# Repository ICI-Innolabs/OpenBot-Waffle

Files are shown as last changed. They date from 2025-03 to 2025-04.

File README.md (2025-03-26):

# Welcome to the OpenBot Waffle repository!

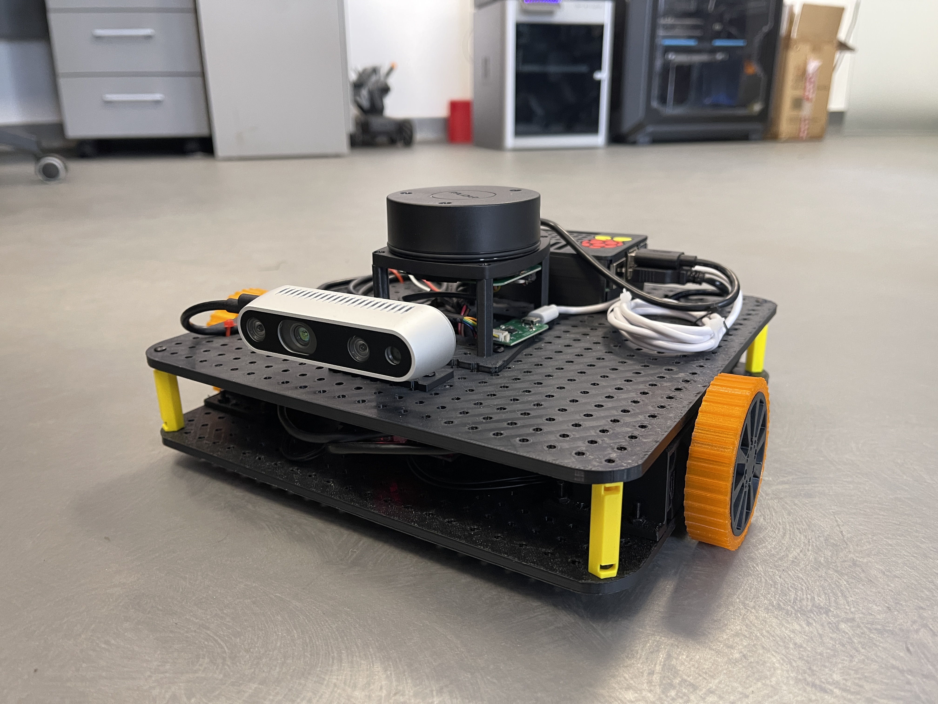
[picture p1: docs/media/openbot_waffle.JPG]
ICIBot Waffle


OpenBot Waffle is a ROS2-based robot platform that can be used for research, education, and hobby purposes. The robot is built around ROS2 and uses a Raspberry Pi 5 as the main controller. The robot is equipped with a Dynamixel XL430-W250-T motor, a Slamtec A1 Lidar, an Adafruit BNO055 IMU, and an Intel RealSense D435i depth camera. The structure of the robot is 3D printed and can be easily assembled. To make things easier when trying new things, the robot can be simulated in Gazebo.

Out of the box, the robot can be controlled via a keyboard or joystick. Also it can also perform SLAM (Simultaneous Localization and Mapping) using Nav2 package from ROS2. 

## 3D Preview

To preview the 3D model of the robot, you can use the following link: [OpenBot Waffle 3D Preview](https://cad.onshape.com/documents/e4455d89093a44267b1c8add/w/d262dbe7157cadda162aa249/e/e17b02729e8f8845fbf66276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)

# Instructions

## Printing and Assembly

To build the OpenBot Waffle robot, you will need to 3D print the components and assemble them. The components list can be found here: [List of Components Needed to Build OpenBot Waffle](docs/component_list.md). The 3D printing and assembly instructions can be found here: [Printing and Assembling Instructions for OpenBot Waffle](docs/3d_printing.md).

## Installation

- After building the physical robot, you will need to install the software on the Raspberry Pi 5. The software installation instructions can be found here: [Software Installation Instructions for OpenBot Waffle](docs/software_installation.md).

- If you are new to ROS2 we recommend you to take a look at the basic instructions here: [ROS2 Basic Instructions](docs/ros2_basic.md).

- When you have ROS2 installed proceed with the next intructions to learn how to launch the robot's main packages and teleoperate the robot: [OpenBot Waffle Basics](docs/teleoperation.md).

## SLAM and Navigation

- To perform SLAM (Simultaneous Localization and Mapping) and start navigation with the robot, you can follow the instructions here: [SLAM and Navigation with OpenBot Waffle](docs/slam.md).

## Gazeebo Simulation

- The robot can be simulated in Gazebo. To simulate the robot in Gazebo, you can follow the instructions here: [Gazebo Simulation for OpenBot Waffle](docs/gazebo_simulation.md).

## Preview of the main packages:

### BNO055_Driver
 - package cloned from https://github.com/the-hive-lab/bno055_driver 
 - to run independently the node that publishes the imu topic: ``` ros2 launch bno055_driver imu.launch.py ``` 
 - publishes in /imu topic

### Dynamixel_Hardware
 - package cloned from https://github.com/dynamixel-community/dynamixel_hardware/tree/jazzy (make sure clone branch jazzy)
 - hardware interface pacage for dynamixel motors
 - used for the dynamixel controller node

### imu_odom_fusion
 - package that fuses the imu and odometry data to publish the robot's pose
 - to run independently the node that publishes the robot's pose: ``` ros2 launch imu_odom_fusion ekf_launch.py ```
 - fusions using extended kalman filters imu readings from imu topic and odometry estimates from odom topic (published by the diff_drive_controller node based on wheel encoders) 
 - publishes in /odometry/filtered topic

### urdf_description
 - package that contains the robot's urdf description, differential drive controller and robot launch files
 - to publish the robot's urdf description: ``` ros2 launch urdf_description urdf_visualize.launch.py ```
 - to launch the robot launch file: ``` ros2 launch urdf_description robot.launch.py ```
    - launches the diff_drive_controller node that publishes the robot's odometry and listens to the cmd_vel topic to control the robot's movement
    - launches the joint_state_publisher node that publishes the robot's joint states
    - can launch the robot_state_publisher node that publishes the robot's tf tree (commented by default)
    - launches joint_state_bridge node that publishes the joint states in the /joint_states topic
    - launches lidar node that publishes the lidar data in the /scan topic (by default from /dev/ttyUSB1)
    - launches the imu_odom_fusion node that fuses the imu and odometry data to publish the robot's pose

### teleop_twist_keyboard
 - package cloned from https://github.com/ros-teleop/teleop_twist_keyboard
 - modified to work with twist stamped messages
 - to run the node that publishes the twist stamped messages: ``` ros2 run teleop_twist_keyboard teleop_twist_keyboard ```

### mapping
 - package that contains the launch file to run cartographer and the configuration files
 - to run cartographer: ``` ros2 launch mapping cartographer.launch.py ```
 - to publish the map: ``` ros2 launch mapping nav2_map_server.launch.py ``` (ignore if use the launch file from localization package)

### localization
 - package that contains the launch file to run amcl and the configuration files
 - to run amcl: ``` ros2 launch localization localizer.launch.py ```

### path_planning
 - package that contains the launch file to run nav2 path planning and the configuration files
 - to run nav2: ``` ros2 launch path_planning path_planner.launch.py ```

### openbot_waffle_gazebo
 - package that contains the launch file to run the gazebo simulation
 - to run the gazebo simulation: ``` ros2 launch openbot_waffle_gazebo robot_description_gazebo.launch.py ```

# License

This project is licensed under the MIT License. See the LICENSE file for details.

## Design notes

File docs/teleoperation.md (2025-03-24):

# Openbot Waffle base packages and teleoperation

This instruction will guide you through the process of getting the robot up and running with the main packages and how to teleoperate the robot via the keyboard or joystick. Also, it will show you how to visualize the robot in RVIZ2.

This project uses ROS2 Control in combination with a custom hardware interface based on the [dynamixel_hardware](https://github.com/dynamixel-community/dynamixel_hardware/tree/jazzy) package that listens for TwistStamped messages on the `/cmd_vel` topic and sends velocity commands to the Dynamixel motors.

## Prerequisites to launch the robot main packages

Firstly on the computer where you will run RVIZ2 launch the robot state publisher node that publishes the robot's tf tree. This can be done by running the following command:

```
ros2 launch urdf_description urdf_visualize.launch.py
```

Then on the Raspberry Pi (robot), launch the robot launch file that starts the diff_drive_controller node that publishes the robot's odometry and listens to the `/cmd_vel` topic to control the robot's movement. This can be done by running the following command:

```
ros2 launch urdf_description robot.launch.py
```

### What does this launch file do?

- Launches the diff_drive_controller node that listens to the `/cmd_vel` topic to control the robot's movement
- Launches the joint_state_publisher node that publishes the robot's joint states to the `/joint_states` topic
- Launches the imu_node that publishes the imu data from BNO055 sensor to the `/imu` topic
- Launches the lidar_node that publishes the lidar data from the RPLidar A1 to the `/scan` topic
- Launches the imu_odom_fusion node that fuses the imu and odometry data to publish the robot's pose to the `/odometry/filtered` topic
- Launches the realsense2_camera node that publishes the RGB and depth images from the RealSense D435 camera
- Launches the tf2_ros static_transform_publisher node that publishes the static transform between the camera and the robot's base_link frame

If all the nodes are launched successfully, you should see the robot's URDF model in RVIZ2 and be able to control the robot using the teleop_twist_keyboard node following the instructions below. If you didn't connect the Lidar or the IMU sensor you should expect to see specific errors in the terminal but the robot should still be able to move. 

### How to visualize the robot in RVIZ2?

To visualize the robot in RVIZ2, run the following command in a new terminal:

```
rviz2
```

When RVIZ2 starts, click on the "Add" button in the bottom left corner of the window and RobotModel. To be able to see the robot set the robot description to /robot_description and the fixed frame to odom. In the next image, you can see the robot in RVIZ2 (refer to the images on the left side to see the settings for the RobotModel).

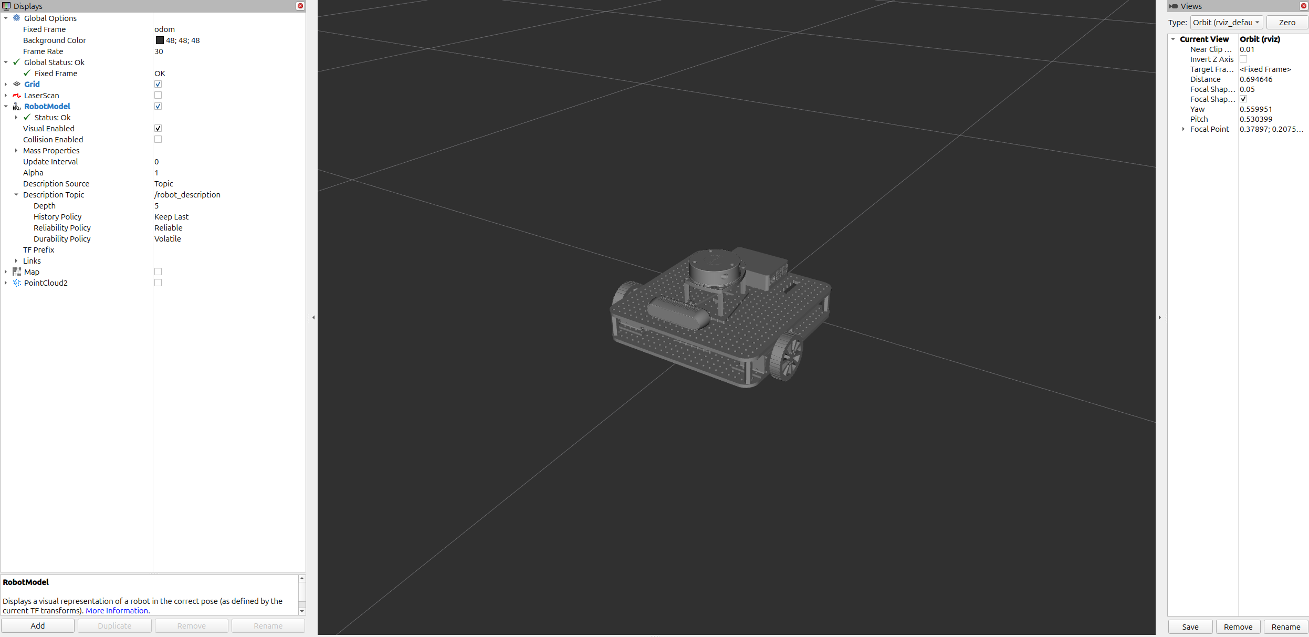
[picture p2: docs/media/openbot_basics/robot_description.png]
OpenBot Waffle in RVIZ2
 

To see the scans from the Lidar, add by topic the lidar scans. To see the camera images, add by topic the PointCloud2 under camera/camera/depth/color/points topic. In the next image you can see the robot along with the lidar scans (pink points) and the camera readings (RGB and depth images) projected in the 3D space.

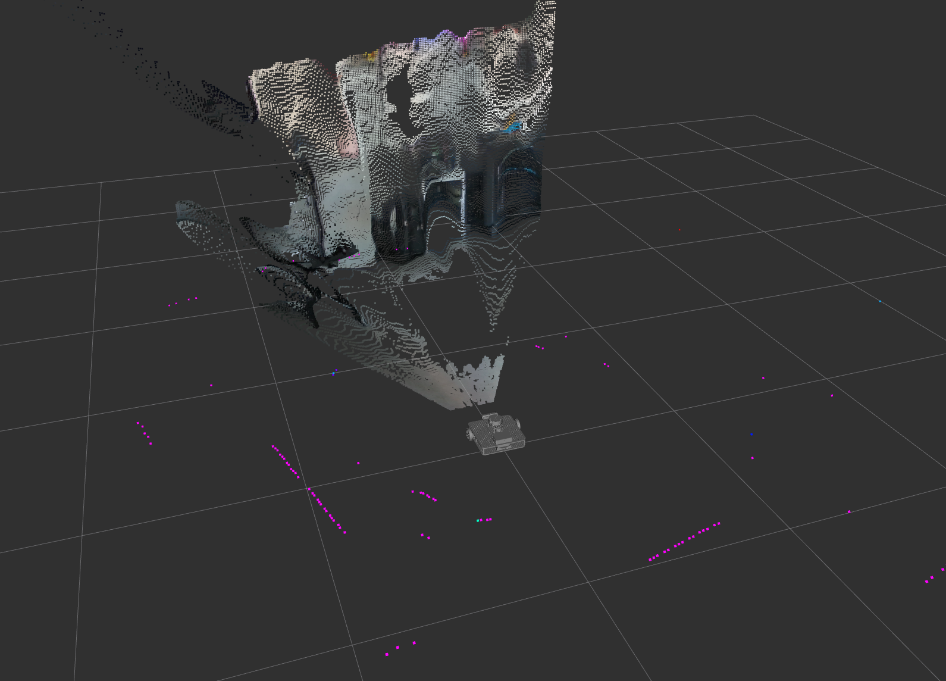
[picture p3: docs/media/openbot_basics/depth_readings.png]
OpenBot Waffle in RVIZ2 with Lidar and Camera
  

## Keyboard Teleoperation

Teleoperation is provided via a modified version of the [teleop_twist_keyboard](https://github.com/ros-teleop/teleop_twist_keyboard) package that now publishes TwistStamped message to control the robot.

To start teleoperating the robot, run the following command in your terminal:

```
ros2 run teleop_twist_keyboard teleop_twist_keyboard
```

When the node starts, use your keyboard according to the on-screen instructions to control the robot. When pressing 'i' the robot will move forward, ',<' to move backward, 'j' to rotate left, and 'l' to rotate right and 'k' to stop the robot.

You can also publish TwistStamped messages directly to the `/cmd_vel` topic to control the robot. For example, to move the robot forward at a linear velocity of 0.1 m/s and an angular velocity of 0.1 rad/s, run the following command:

```
ros2 topic pub /cmd_vel geometry_msgs/msg/TwistStamped '{
  header: {
    stamp: { sec: 0, nanosec: 0 },
    frame_id: ""
  },
  twist: {
    linear: { x: 0.1, y: 0.0, z: 0.0 },
    angular: { x: 0.0, y: 0.0, z: 0.1 }
  }
}'
```

## Joystick Teleoperation

Teleoperation can also be done using a joystick. To start teleoperating the robot with a joystick, run the following command in your terminal:

```
ros2 launch urdf_description diff_drive_control.xacro
```

When the node starts, use your joystick to control the robot. The robot will move according to the left joystick and if you want to move the robot faster (boost mode) you can press R2 button.

This node is inspired from Articulated Robotics. 
 - [Youtube Video](https://www.youtube.com/watch?v=F5XlNiCKbrY)
 - [Github Repository](https://github.com/joshnewans/articubot_one/tree/174b3f311ab146ef12c6549ad0640cb985854972)

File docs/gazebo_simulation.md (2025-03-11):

# Gazebo Simulation

## How to start the simulation

To start the simulation, after building and sourcing the project, simply run the command:
```
ros2 launch openbot_waffle_gazebo robot_description_gazebo.launch.py
```

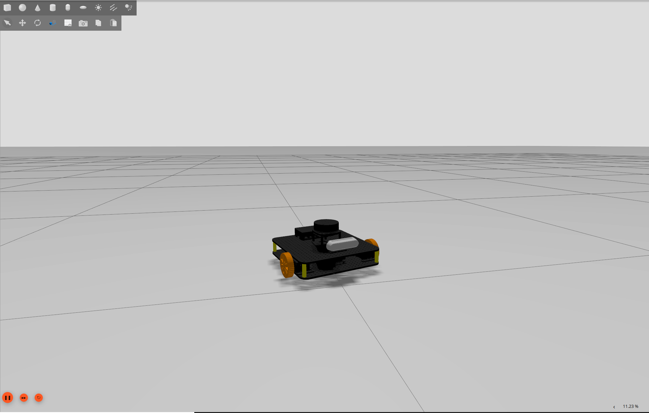
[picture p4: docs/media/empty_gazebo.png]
ICIBot Waffle in empty Gazebo World


- this will launch the Gazebo Simulator and will spawn the OpenBot Waffle into an empty world (as in the  image above)
- it bridges multiple topics from gazebo to ros2 to be able to view in Rviz2 what is the perception of the robot 
- to control the robot using "wasdx" keys from the keyboard, add in gazebo the key publisher from the top right dropdown after searching for it (as in the next image)

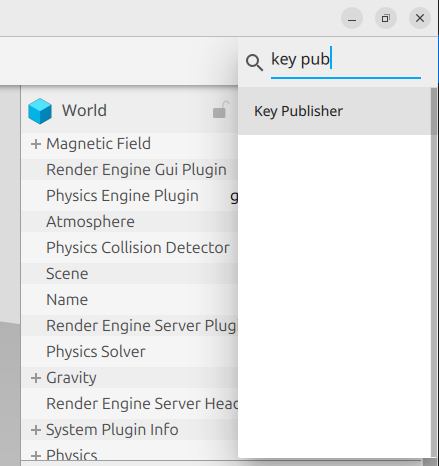
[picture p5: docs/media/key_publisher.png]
Key publisher drop down Gazebo


## Lidar and Depth camera

- similar to the key publisher, lidar visualization can be added in gazebo (do no forget to select the topic where the scans are published, in our case /lidar)
- after adding a few objects into the Gazebo World (similar to next figure), open rviz2 from a new terminal.

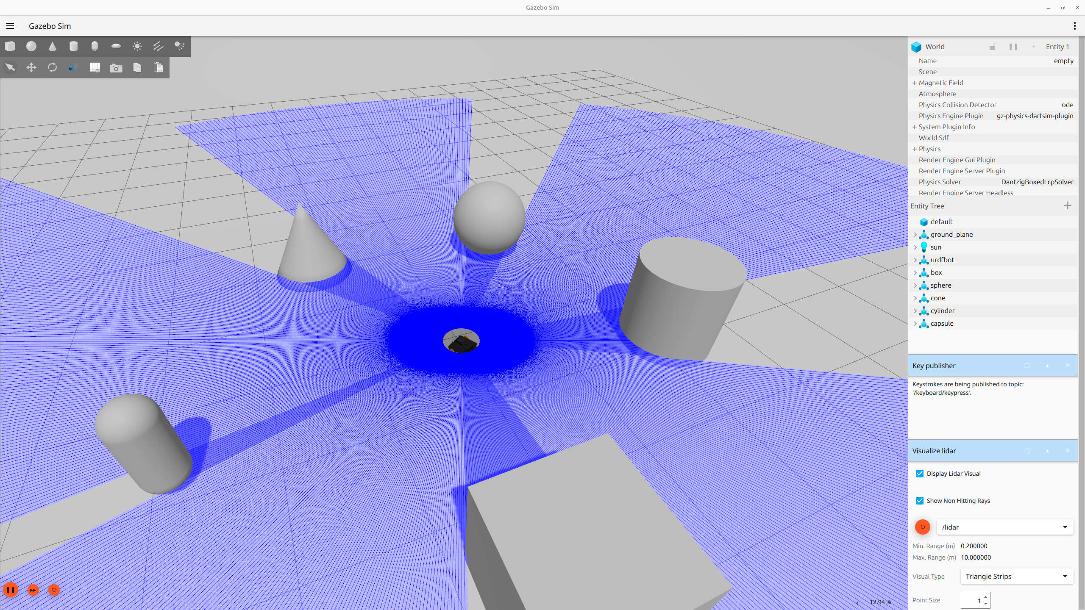
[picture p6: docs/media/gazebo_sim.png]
ICIBot Waffle in empty Gazebo World


- add by topic in rviz2 the PointCloud2 depth readings from the simulated depth camera and the LaserScans from the lidar.

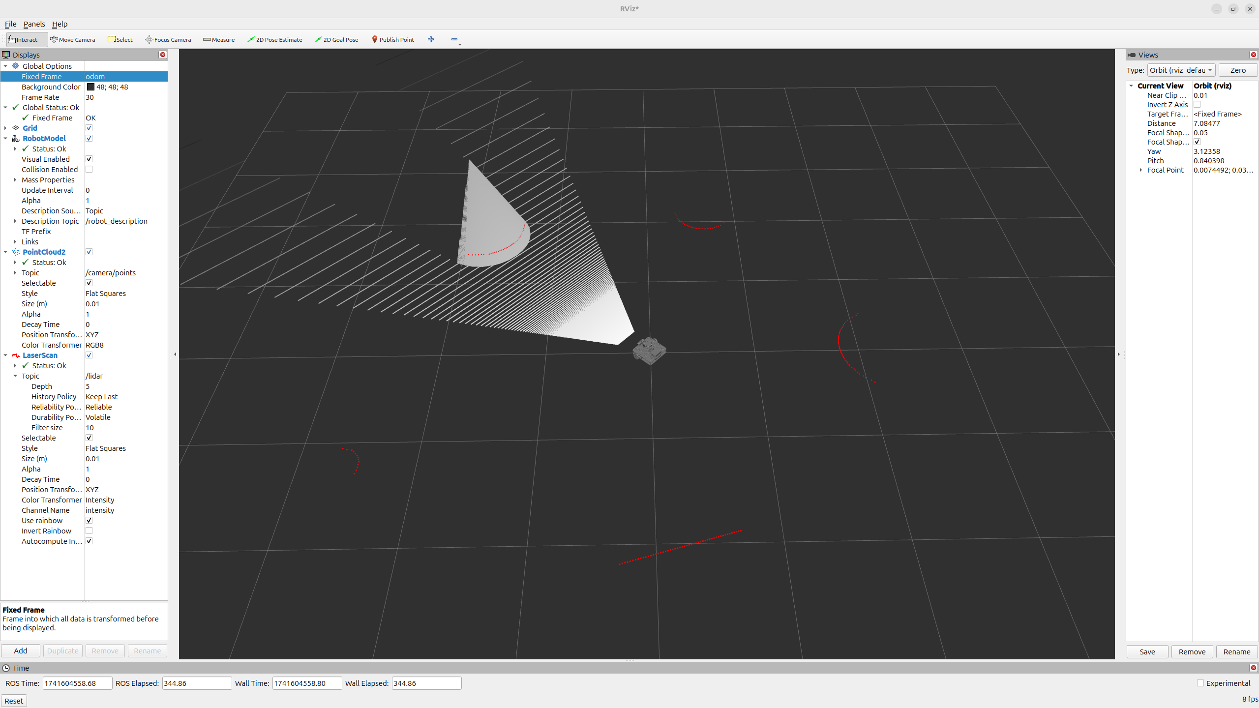
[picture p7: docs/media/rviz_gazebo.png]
Rviz2 Visualization


- you can observe how the readings from the lidar and the depth camera match each other. In our example, the robot is facing the cone and we can see the readings of the lidar are projected as expected on the cone, on level with the lidar of the robot.
- if you move the robot you can observe how the robot moves and the objects remain in the same spots on the visualization (make sure to use as fixed frame /odom in Rviz2)

## Extra

### Gazebo commands

 - To list all the gazebo topic run

```
gz topic -l
```

 - To view the informations about a specific topic (in this case /scan):
 
```
gz topic -t /scan -i
```
 - To echo a topic  (in this case /scan):
 
```
gz topic -t /scan -e
```
 - To publish messages in a topic (in this case in /cmd_vel)
 
```
gz topic -t /cmd_vel -m gz.msgs.Twist -p '
linear: { x: 0.2, y: 0.0, z: 0.0 }
angular: { x: 0.0, y: 0.0, z: 0.0 }'
```

### Bridging

Since we are using Gazebo Sim, to have a topic from ros2 to gazebo or from gazebo to ros2 we have to bridge them manually. When bridging a topic we have to specify the name of the topic and the type of messages (for both ros2 and gz) and the direction of the bridge. The Ros2 and Gz message type correspondets and be viewed [here](https://github.com/gazebosim/ros_gz/blob/ros2/ros_gz_bridge/README.md). Official docs: [here](https://gazebosim.org/docs/latest/ros2_integration/).

to bridge camera topic from gz to ros2: 
```
ros2 run ros_gz_bridge parameter_bridge /camera@sensor_msgs/msg/Image[gz.msgs.Image
```

### More

Official tutorial for simulating a differential steering robot in Gazebo:  https://gazebosim.org/docs/latest/building_robot/

Template for integrating ros2 and gazebo: https://github.com/gazebosim/ros_gz_project_template

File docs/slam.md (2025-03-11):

# Simultaneous Localization and Mapping (SLAM) Example with OpenBot Waffle

## Prerequisites

 - make sure that you've followed the [instructions for teleoperation and robot diff drive control](teleoperation.md) in order to be able to move the robot around

 - publish the robot's urdf description (preferably from external pc to be able to use Rviz2 with higher FPS) with: 
 ``` 
 ros2 launch urdf_description urdf_visualize.launch.py 
 ```

 - launch the robot launch file (directly from raspberry pi): 
 ``` 
 ros2 launch urdf_description robot.launch.py 
 ```

  - make sure thath the robot is publishing the odom topic and the lidar scans. This can be checked by running the next command and looking for /odom and /scans topics 
 ``` 
 ros2 topic list 
 ``` 

 - open a new terminal and launch rviz2: 
 ```
 rviz2 
 ```

 - add the robot model in rviz2 by clicking the Add button and selecting RobotModel. For the moment make sure that the Fixed frame is set to /odom or /base_link.

 - add the LaserScan by topic to visualize the lidar scans.

## Mapping
 - the scope of this is to create the map of the environment where the robot will navigate

 - to launch the cartographer node that will map your environment simply run: 
 ``` 
 ros2 launch mapping cartographer.launch.py 
 ```
 - after launching this node, the robot will start mapping the environment. The map can be visualized in rviz2 by adding the map topic. Make sure that in rviz2 the Fixed frame is set to /map, map topic is set to /map, the history policy to Keep Last, Reliability to Reliable and Durability Policy to Transient Local. In the next image you can see how the map looks when the robot starts mapping the environment. 

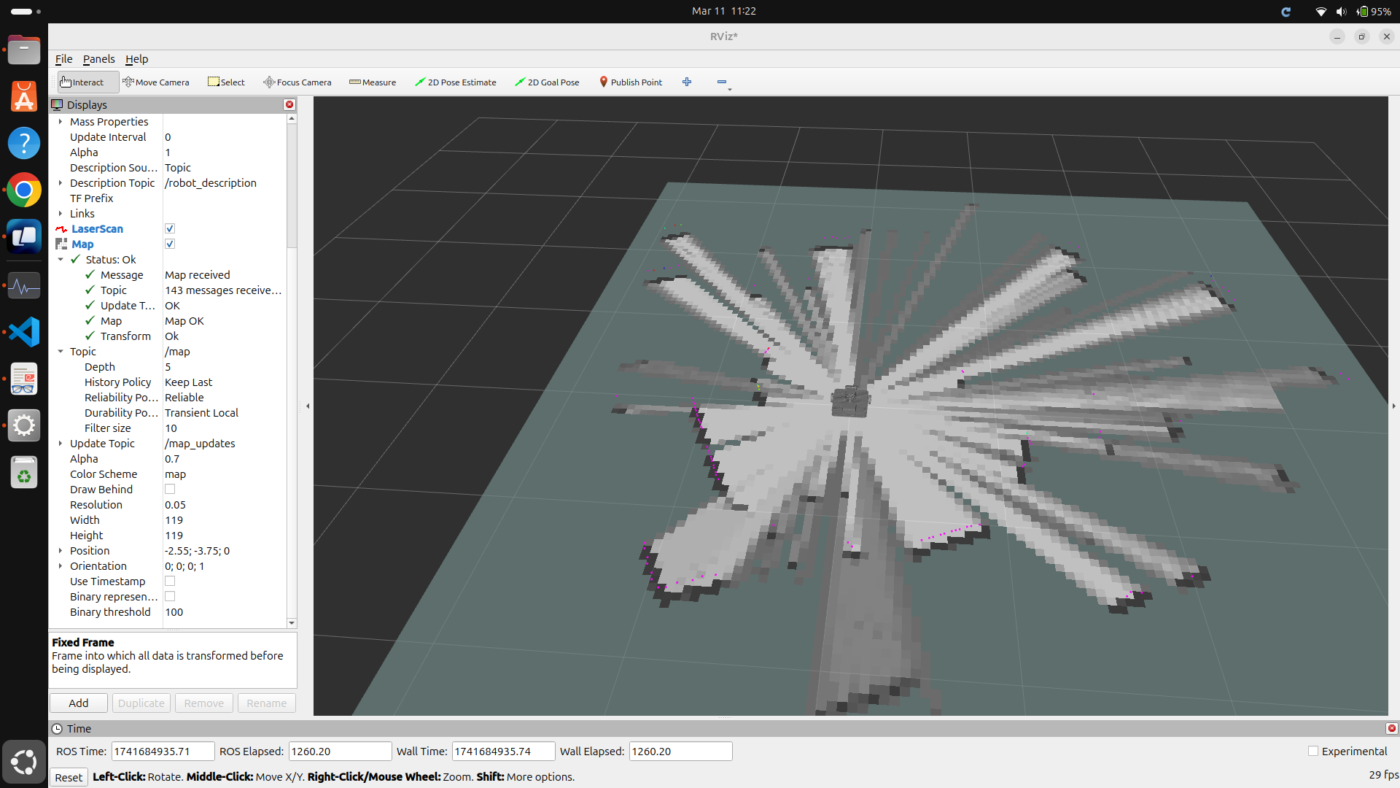
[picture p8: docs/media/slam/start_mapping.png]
Start Mapping Rviz2
 

 - to map the environment the robot needs to moved around. This can be done by teleoperating the robot with the teleop_twist_keyboard node that can be launched with the next command: 
 ``` 
 ros2 run teleop_twist_keyboard teleop_twist_keyboard 
 ``` 

 - after covering the entire environment, the map should look similar to the next image. We suggest to move the robot in a way that the entire environment is covered and have as little as possible dynamic objects in the environment.

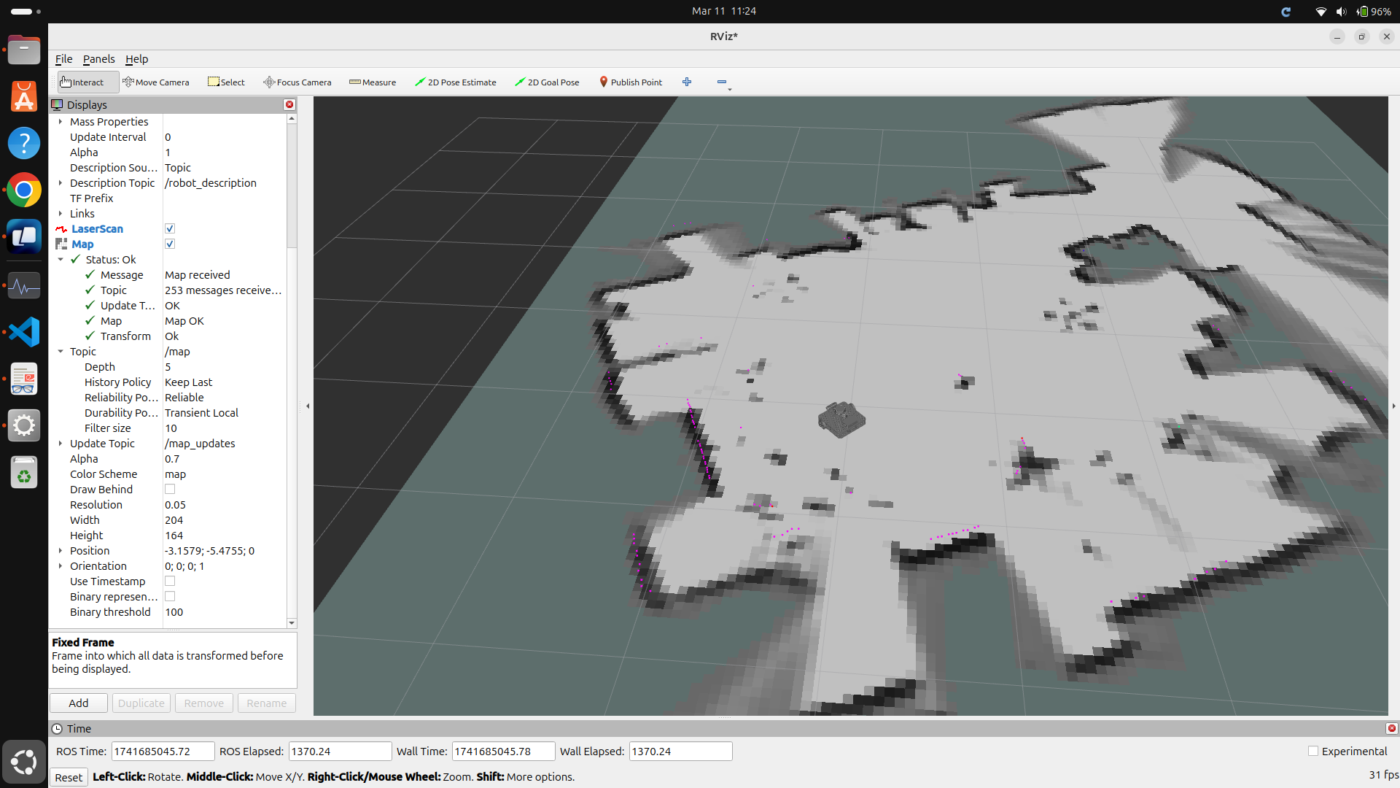
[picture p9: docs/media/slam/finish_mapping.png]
End Mapping Rviz2
  

 - after you've completed mapping the environment, navigate into the config folder inside the mapping package and run the next command to save the map: 
 ``` 
 ros2 run nav2_map_server map_saver_cli -f <path_to_save_map> 
 ```

 - if you want to publish the map this can be done with the following command (ignore if use the launch file from localization package): 
 ``` 
 ros2 launch mapping nav2_map_server.launch.py 
 ``` 

## Localization
 - to localize the robot in the environment, the amcl (Adaptive Monte Carlo Localization) from nav2 package is used.

 - make sure that the name of the saved map is corectly set in the localization package launch file (localizer.launch.py).

 - launch the amcl node: 
 ``` 
 ros2 launch localization localizer.launch.py 
 ```

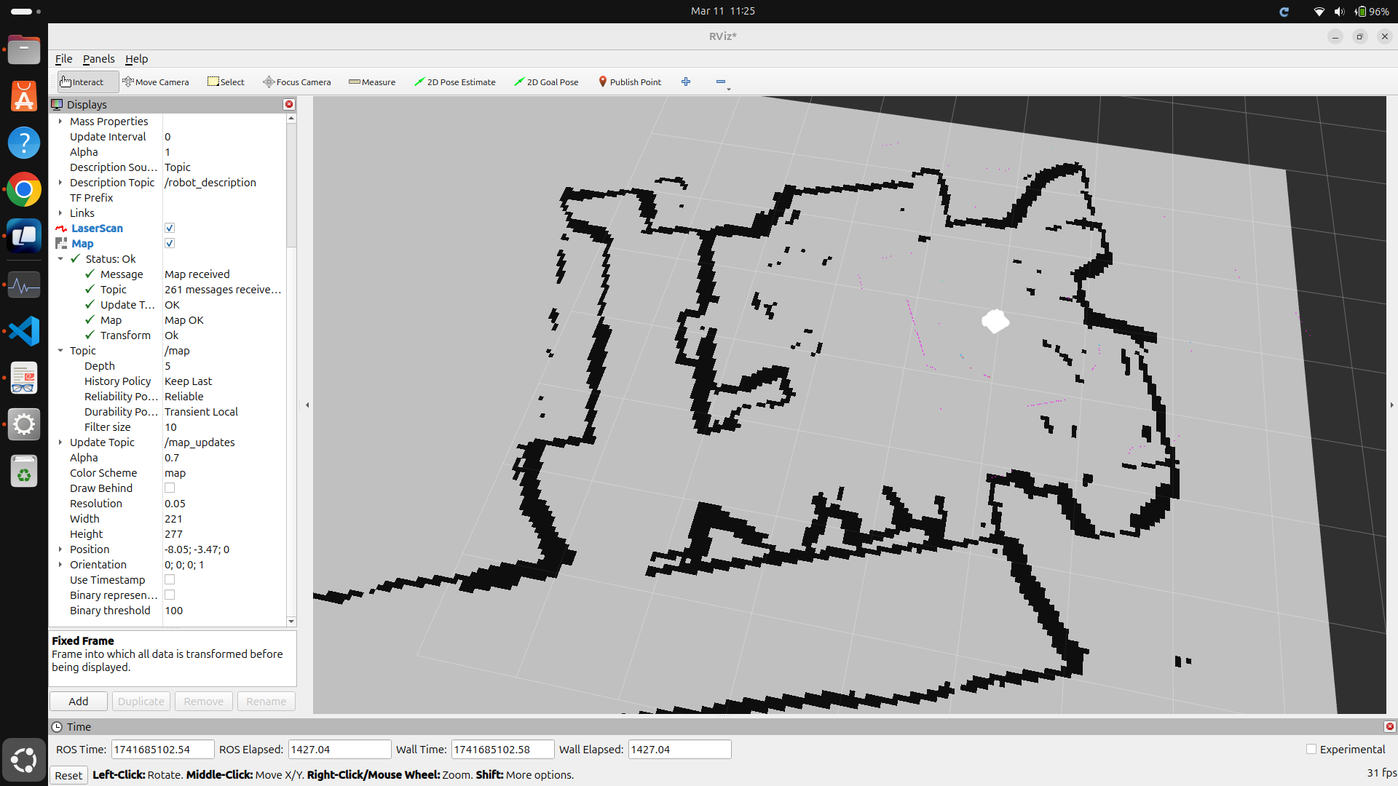
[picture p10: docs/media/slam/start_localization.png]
Start Localization Rviz2
  

 - after launching this node, the robot will wait for the initial pose to be set. This can be done by clicking the 2D Pose Estimate button in rviz2 and setting the initial pose of the robot. Try to set the initial pose as close as possible to the real pose of the robot.

 - after setting the initial pose, the robot will start localizing itself in the environment. The estimated pose can be visualized in rviz2 by adding the PoseWithCovariance by topic. To better localize the robot, you can move the robot around  the environment. After giving the 2D Pose we suggest to simply rotate the robot in place to see how the robot drifts on the map till it localizes itself. When the robot localized itself correctly the lidar scans will match the map (view next image).

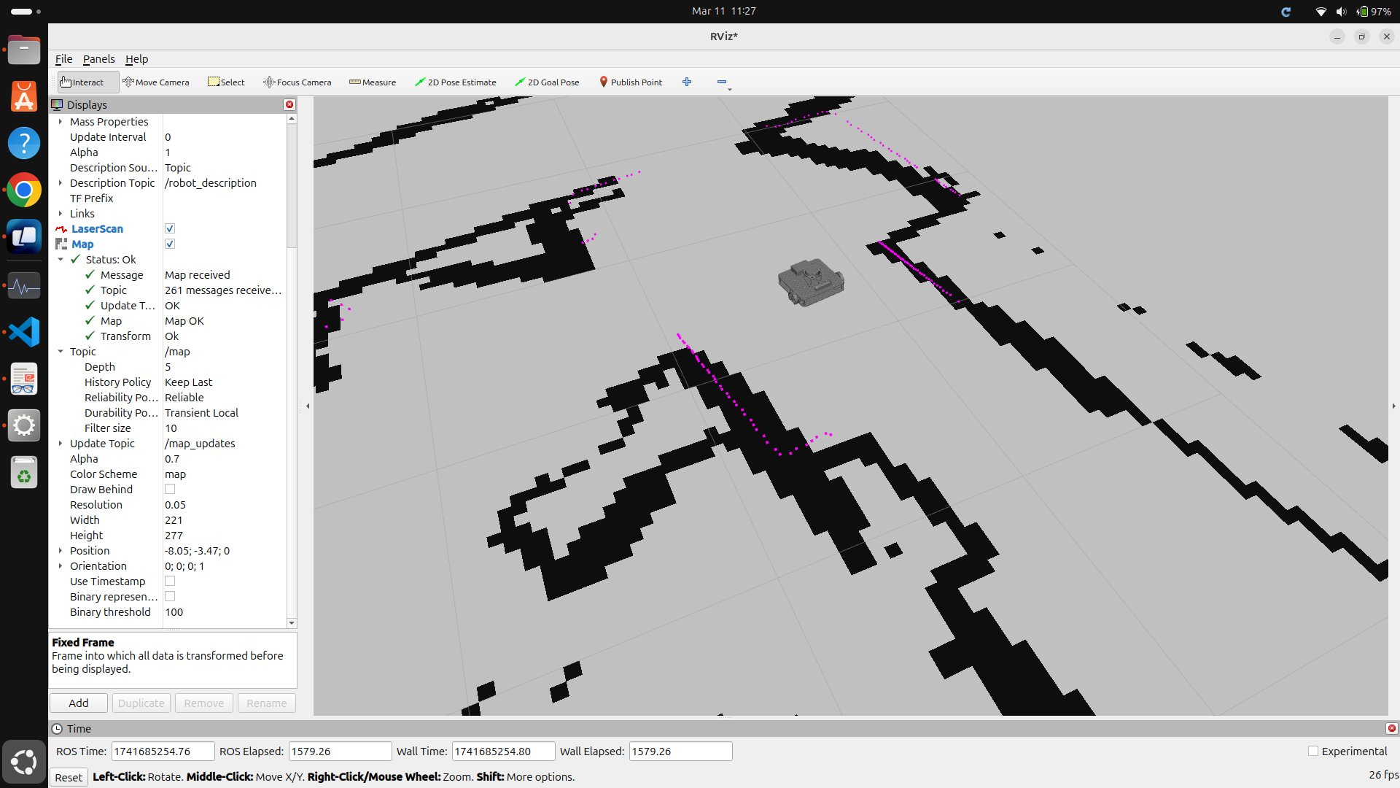
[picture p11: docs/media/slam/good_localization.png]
Good localization Rviz2
  

 - when the robot is localized corectly you can move to the path planning step.

## Path Planning
 - to plan the path for the robot, the nav2 package is used.

 - to run the path planning node: 
 ``` 
 ros2 launch path_planning path_planner.launch.py 
 ```

 - to better view what is happening you can add by topic in Rviz2 the local costmap, global costmap, and the planned path and the goal pose.

 - in the next image can be seen the global costmap (in gray) and the local costmap (in colors)

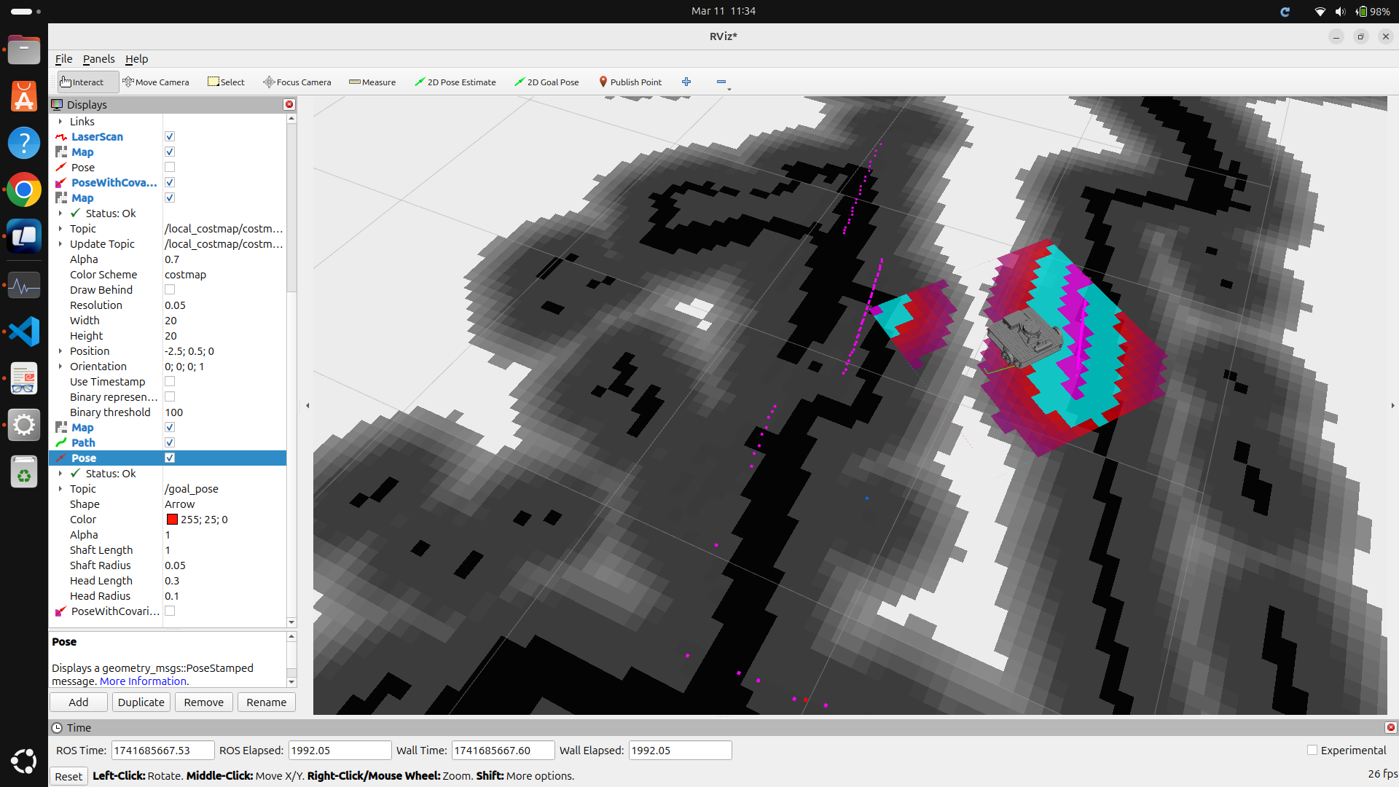
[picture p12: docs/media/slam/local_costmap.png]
Local and Global costmaps in Rviz2
 

 - after launching this node, the robot will wait for the goal to be set. This can be done by clicking the 2D Nav Goal button in rviz2 and setting the goal pose of the robot. Now the robot will start planning the path to the goal and will start moving towards it.

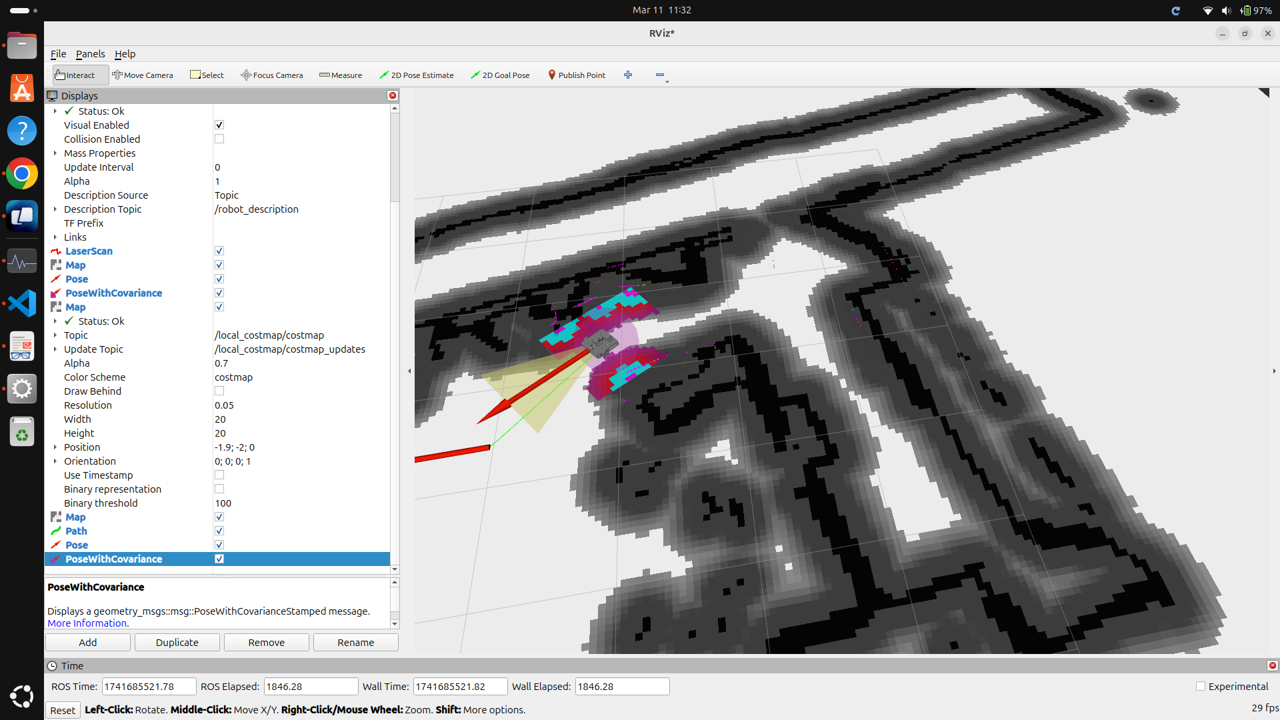
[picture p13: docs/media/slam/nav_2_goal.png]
Navigation to 2D Goal Pose in Rviz2
 

 - in the terminal were you've launched the path planning node, you will see the updated the status of navigation.

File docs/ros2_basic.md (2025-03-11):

# ROS2 Basic commands

Always before running any ROS2 commands, make sure you have sourced both your ROS2 installation and your workspace setup files. In our case, we are using ROS2 Jazzy distribution and the workspace is called `openbot_waffle`. 

``` 
    source /opt/ros/jazzy/setup.bash
    source ~/openbot_waffle/install/setup.bash
```

## Topics

 - to view all active topics in the current ROS2 network, use:
``` 
    ros2 topic list
```

- to inspect the messages being published on a particular topic, use the ros2 topic echo command. For example, to see the output of your lidar data (assuming the topic is named /scan):

``` 
    ros2 topic echo /scan
```

- to get detailed information about a specific topic (including its message type and publisher/subscriber details), use:
``` 
    ros2 topic info /scan
```

- to publish a message on a topic, use the ros2 topic pub command. For example, to publish a message on the /cmd_vel topic (assuming the message type is geometry_msgs/Twist), use:
``` 
    ros2 topic pub /cmd_vel geometry_msgs/Twist '{linear: {x: 0.1, y: 0.0, z: 0.0}, angular: {x: 0.0, y: 0.0, z: 0.1}}'
```

## Nodes

- to view all active nodes in the current ROS2 network, use:
``` 
    ros2 node list
```

- to get detailed information about a specific node (including its name, namespace, and associated topics), use:
``` 
    ros2 node info /node_name
```

- to kill a node, use:
``` 
    ros2 node kill /node_name
```

## Packages

- to list all installed packages in the current ROS2 workspace, use:
``` 
    ros2 pkg list
```

- to create a new python package, use:
``` 
    ros2 pkg create --build-type ament_python package_name
```

- to create a new C++ package, use:
``` 
    ros2 pkg create --build-type ament_cmake package_name
```

- to build a specific package, use:
``` 
    colcon build --packages-select package_name
```

- or alternatively, to build all packages in the workspace, use:
``` 
    colcon build
```

- always remember to source the workspace setup file after building a new package:
``` 
    source ~/openbot_waffle/install/setup.bash
```

## Launch files

- to run a launch file, use:
``` 
    ros2 launch package_name launch_file_name.launch.py
```

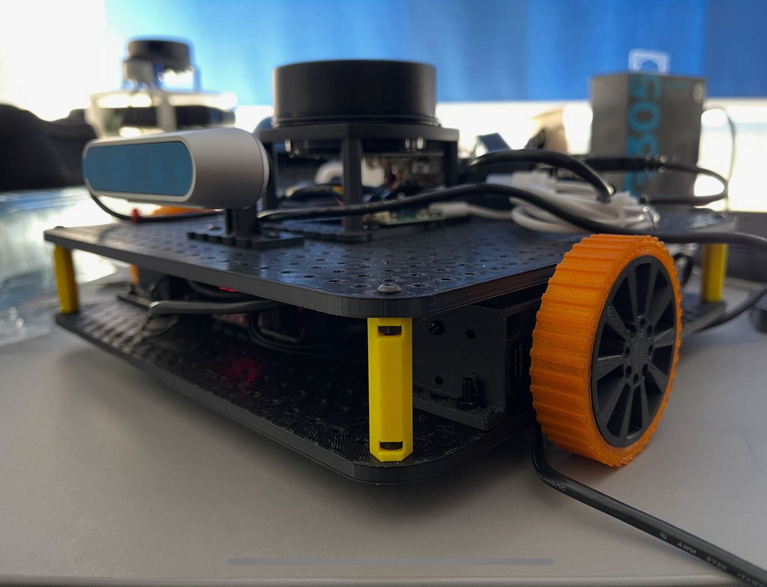
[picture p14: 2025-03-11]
docs/media/icibot_waffle.jpeg

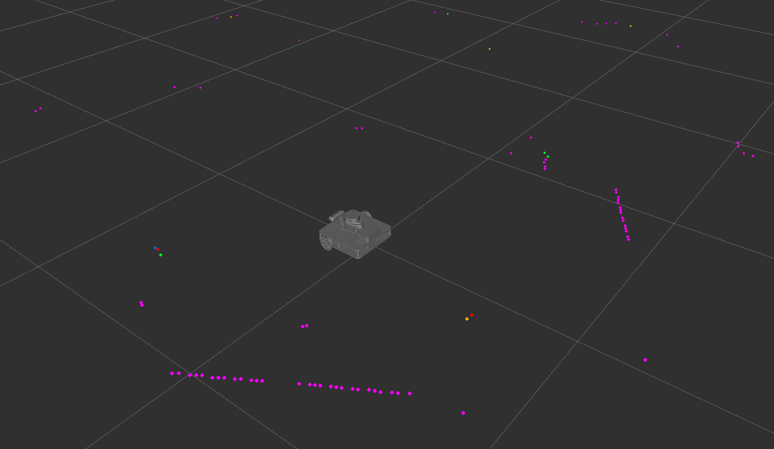
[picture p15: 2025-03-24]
docs/media/openbot_basics/lidar_scans.png

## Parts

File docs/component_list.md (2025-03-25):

# List of Components Needed to Build OpenBot Waffle

| Component | Link | Quantity | Price (single unit) |
| --- | --- | --- | --- |
| Dynamixel XL430-W250 T | [Dynamixel XL430-W250-T Servo](https://www.generationrobots.com/en/402823-dynamixel-xl430-w250-t-servomotor.html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) | 2 | 57 € |
| U2D2 Connector | [U2D2 Dynamixel/PC Connector](https://www.generationrobots.com/en/402820-u2d2-dynamixelpc-connector.html) | 1 | 56 € |
| U2D2 PHB Set | [Génération Robots U2D2 PHB Set](https://www.generationrobots.com/en/403359-u2d2-power-hub-board.html) | 1 | 23 € |
| Raspberry Pi 5 (optimal 8GB version)| [Raspberry Pi 5](https://www.raspberrypi.com/products/raspberry-pi-5/?variant=raspberry-pi-5-8gb) | 1 | 85 € |
| Slamtec A1 Lidar | [RPLIDAR-A1](https://www.slamtec.com/en/lidar/a1) | 1 | 160 € |
| Adafruit BNO055 IMU | [BNO055](https://www.robofun.ro/9-dof-senzor-de-orientare-absoluta-bno055.html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) | 1 | 55 € |
| Depth Camera Intel D435i | [Intel® RealSense™ D435i](https://www.intelrealsense.com/depth-camera-d435i/) | 1 | 400 € |
| 18650 Battery | | 3 | 6 € |
| M3 Screws | | 50 | 5 € |
| M3 Bolts | | 50 | 5 € |
| SD card (at least 32 GB) | | 1 | 10 € |
| 24V/12V to 5V 5A Power Module DC-DC | [Power Module](https://www.optimusdigital.ro/en/step-down-power-supplies/12484-24v12v-to-5v-5a-power-module-dc-dc-xy-3606-power-converter.html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) | 1 | 4 € |

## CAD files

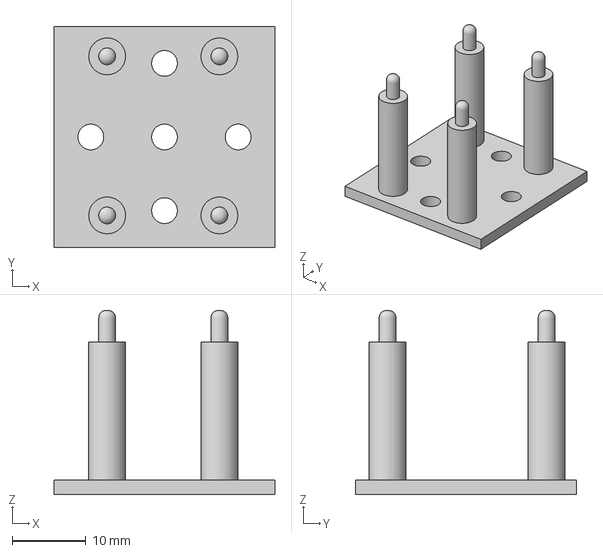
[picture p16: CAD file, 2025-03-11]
3d_files/all_files/IMU Holder.3mf
30.0 x 30.0 x 25.0 mm

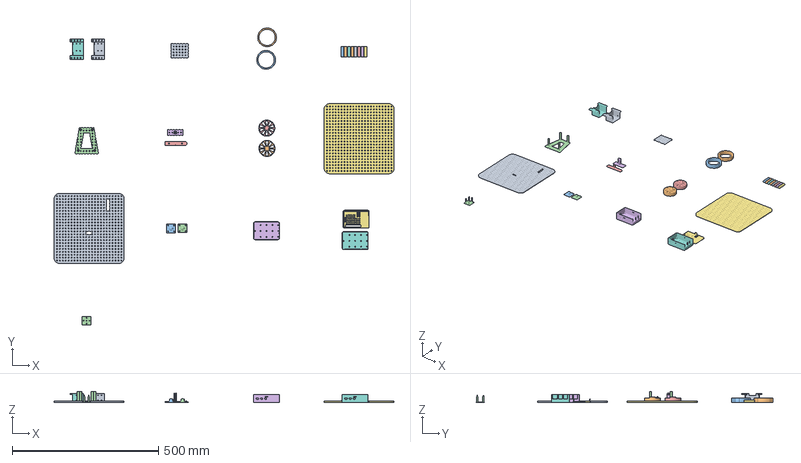
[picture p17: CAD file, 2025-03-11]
3d_files/openbot_waffle_bambu.3mf
1160.7 x 1014.8 x 37.7 mm
U2D2 Holder
tire1 x 2
lidar holder
depth_holder_A
depth_holder_B
baza_lvl_0_B
motor_holder_1 NEW x 2
baza_lvl_0 (1)_B
Distantier_35mm x 8
caster_wheel v1 x 2
rim1_NEW x 2
Caracasa_1 x 2
Carcasa_pi5 v4
IMU Holder

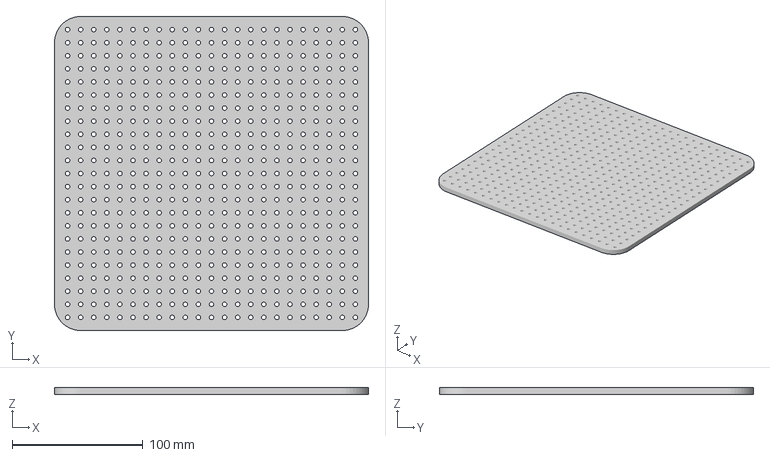
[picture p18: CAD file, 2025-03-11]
3d_files/all_files/base_0.3mf
240.0 x 240.0 x 5.00 mm

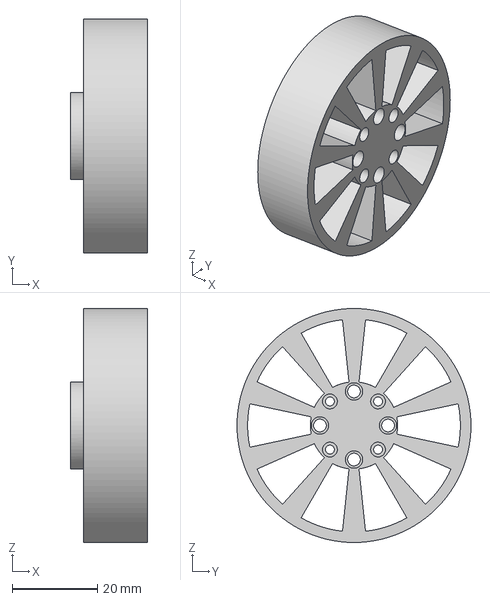
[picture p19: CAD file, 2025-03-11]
3d_files/all_files/rim.3mf
18.0 x 55.0 x 55.0 mm

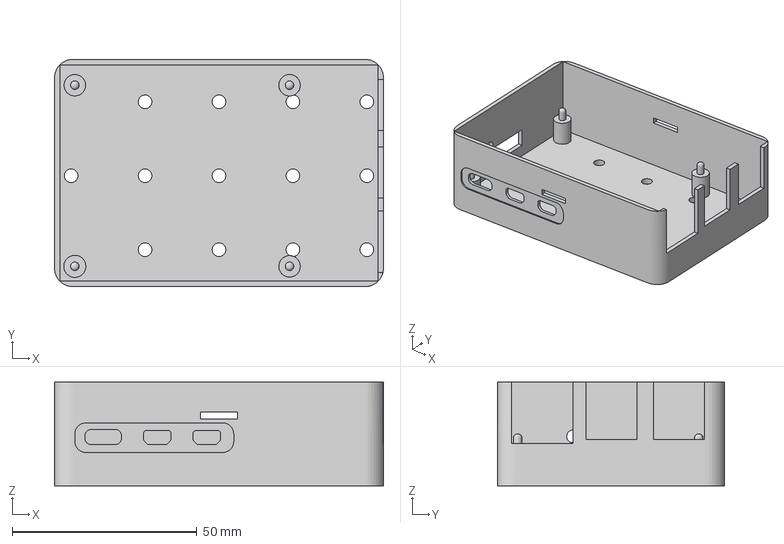
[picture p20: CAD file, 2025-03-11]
3d_files/all_files/pi_case_A.3mf
89.0 x 61.5 x 28.0 mm

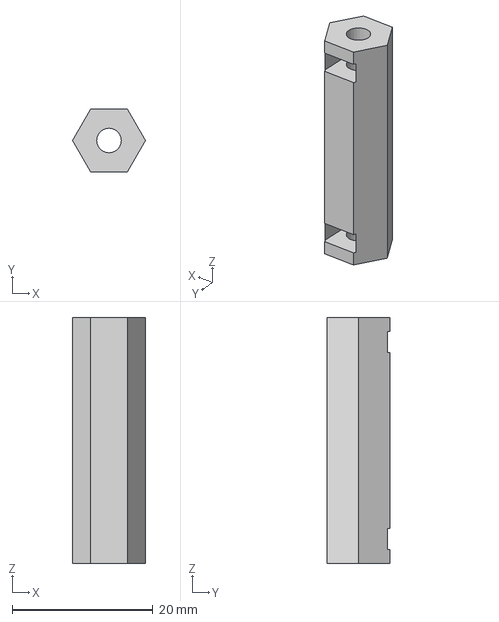
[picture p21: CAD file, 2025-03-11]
3d_files/all_files/spacer_35mm.3mf
10.4 x 9.00 x 35.0 mm

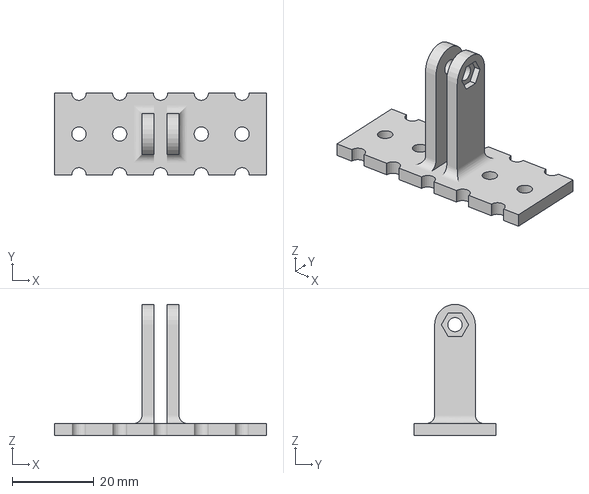
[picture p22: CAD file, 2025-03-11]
3d_files/all_files/dept_holder_B.3mf
52.0 x 20.0 x 32.2 mm

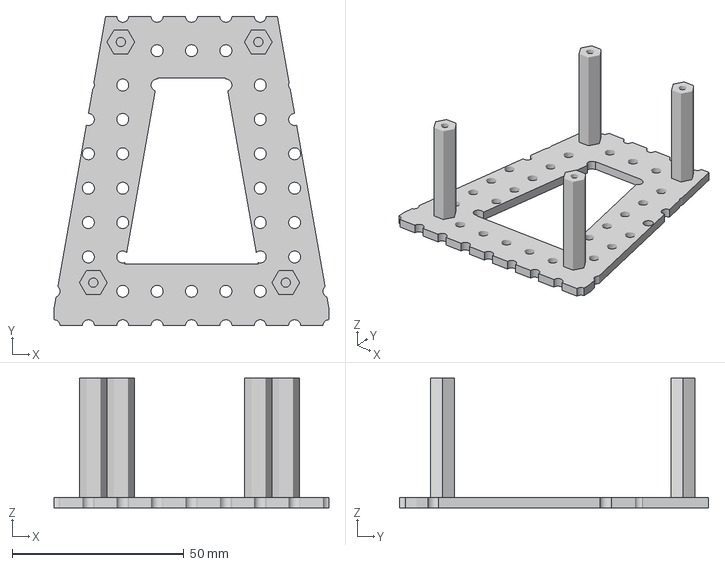
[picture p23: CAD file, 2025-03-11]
3d_files/all_files/lidar_holder.3mf
80.0 x 90.0 x 37.7 mm

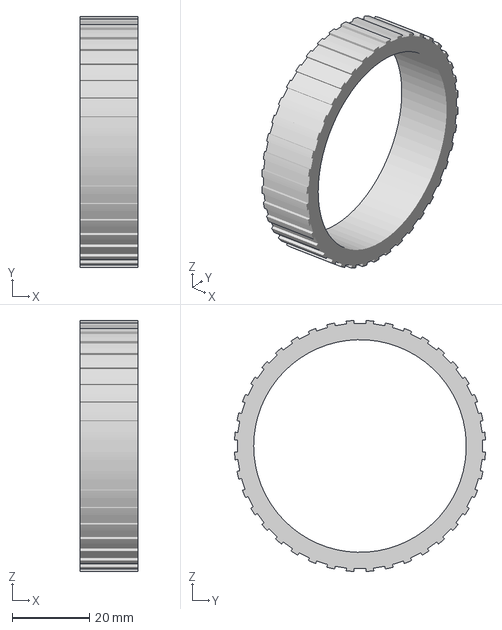
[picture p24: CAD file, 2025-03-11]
3d_files/all_files/tire.3mf
15.0 x 64.9 x 64.9 mm

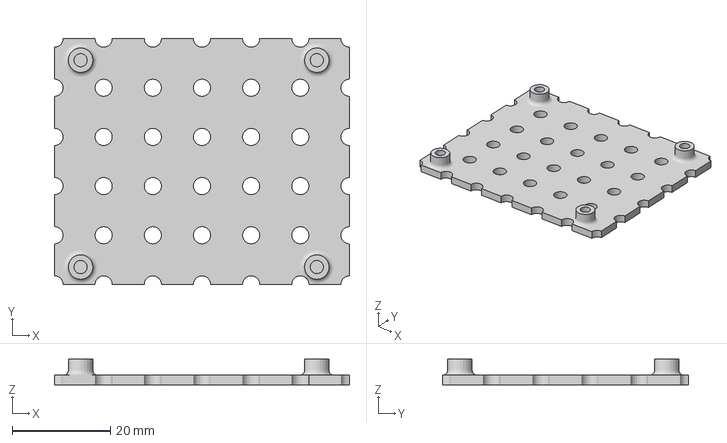
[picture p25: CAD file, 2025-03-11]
3d_files/all_files/holder_u2d2.3mf
60.0 x 50.0 x 5.28 mm

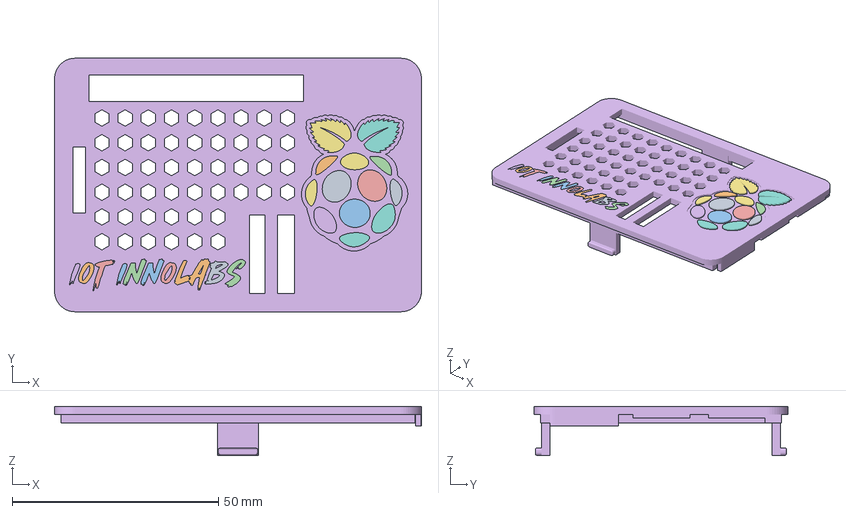
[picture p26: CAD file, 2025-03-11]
3d_files/all_files/pi_case_B.3mf
89.0 x 61.5 x 12.0 mm
Capac_gauri
rpi_frunza (1)
rpi_frunza

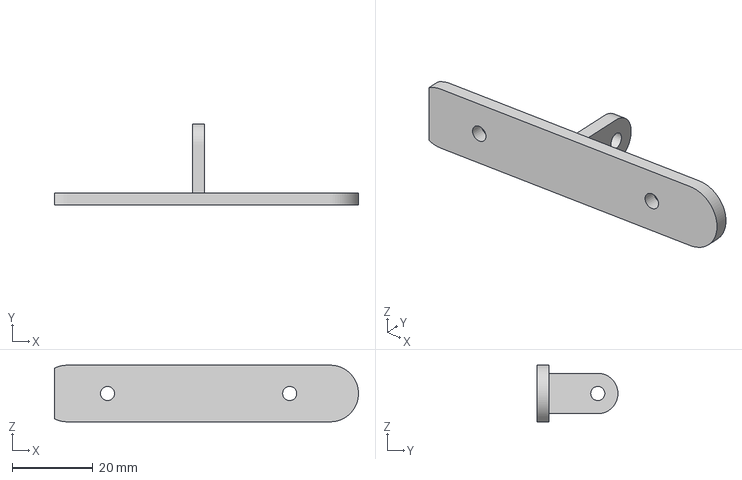
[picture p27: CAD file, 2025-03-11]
3d_files/all_files/depth_holder_A.3mf
75.1 x 20.0 x 14.0 mm

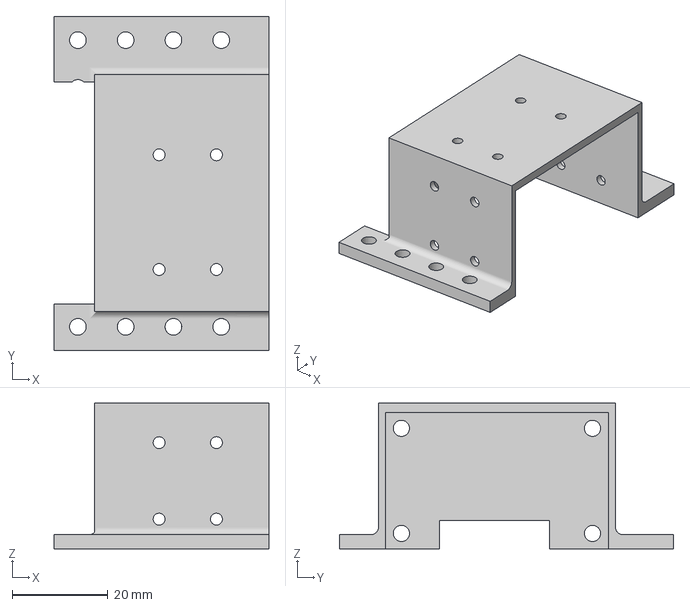
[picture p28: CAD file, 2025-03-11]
3d_files/all_files/xl430_holder.3mf
45.0 x 70.0 x 30.6 mm

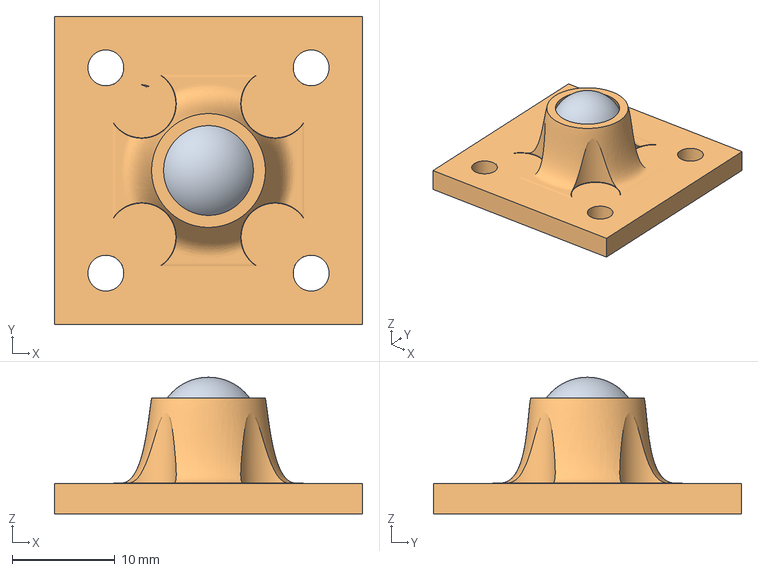
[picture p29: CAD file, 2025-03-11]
3d_files/all_files/caster_wheel.3mf
30.0 x 30.0 x 13.3 mm
object_id_1
object_id_2

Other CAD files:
3d_files/all_files/base1.3mf

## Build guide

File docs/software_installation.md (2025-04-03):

# Software Installation

- Ideally you will be using an external dev machine running Ubuntu 24.04 and ROS2 Jazzy along with the OpenBot Waffle robot that uses a Raspberry Pi 5 running Ubuntu 24.04 and ROS2 Jazzy.
- To install ROS2 Jazzy on Ubuntu 24.04 follow the instructions from the official ROS2 website: [ROS2 Jazzy Installation](https://docs.ros.org/en/jazzy/Installation/Ubuntu-Install-Debs.html)
- Make sure to install the Desktop version of ROS2 Jazzy.
- To install Ubuntu 24.04 on the Raspberry Pi 5, get a new SD card (at least 32 GB), and flash it with Ubuntu using the [Raspberry Pi imager](https://www.raspberrypi.com/software/). After flashing the SD card, insert it into the Raspberry Pi and boot it up. Follow the instructions to set up the Raspberry Pi and proceed with the [installation of ROS2 Jazzy](https://docs.ros.org/en/jazzy/Installation/Ubuntu-Install-Debs.html).
- After installing ROS2 Jazzy, clone the OpenBot Waffle repository to your workspace with the following command:
```
git clone https://github.com/ICI-Innolabs/OpenBot-Waffle.git -b main
```
<!-- - After cloning the repository, also clone the repositories for IMU unit and Dynamixel motors (make sure you clone the jazzy branch) in the `src` folder of your workspace:
```
git clone https://github.com/the-hive-lab/bno055_driver
git clone https://github.com/dynamixel-community/dynamixel_hardware.git -b jazzy
``` -->
- Everything you will run on the Raspberry Pi must be done from the root user. To switch to the root user run the following command (if you will try to launch the node for the imu, it won't work without root permissions):
```
sudo su
```
- Then install the ROS2 packages needed for the OpenBot Waffle robot:
```
sudo apt install ros-jazzy-xacro
sudo apt install ros-jazzy-ros2-control
sudo apt install ros-jazzy-ros2-controllers
sudo apt install ros-jazzy-dynamixel-sdk
sudo apt install ros-jazzy-rplidar-ros
sudo apt install ros-jazzy-joint-state-publisher-gui
sudo apt install ros-jazzy-teleop-twist-keyboard
sudo apt install ros-jazzy-cartographer-ros
sudo apt install ros-jazzy-nav2-amcl
sudo apt install ros-jazzy-nav2-lifecycle-manager
sudo apt install ros-jazzy-nav2-controller
sudo apt install ros-jazzy-nav2-planner
sudo apt install ros-jazzy-nav2-behaviors
sudo apt install ros-jazzy-nav2-bt-navigator
sudo apt install ros-jazzy-nav2-dwb-controller
sudo apt install ros-jazzy-nav2-bringup
sudo apt install ros-jazzy-robot-localization
sudo apt install ros-jazzy-librealsense2*
sudo apt install ros-jazzy-realsense2*
sudo apt install ros-jazzy-dynamixel-workbench-toolbox
sudo apt install ros-jazzy-joint-state-broadcaster
sudo apt install ros-jazzy-diff-drive-controller
sudo apt install ros-jazzy-robot-state-publisher
sudo apt install ros-jazzy-ros-gz-sim
sudo apt install ros-jazzy-ros-gz-bridge
sudo apt install ros-jazzy-nav2-map-server
```

- To install the python packages needed for the OpenBot Waffle, run the following command:
```
pip install -r requirements.txt --break-system-packages
```

## Dynamixel Motors configuration

- To configure the Dynamixel motors firstly connect the motors individually to the U2D2 module and connect the U2D2 to a machine with Dynamixel Wizard 2.0 installed.
- After connecting the first motor change its ID to 1 and the baud rate to 57600.
- Disconnect the first motor then connect the second motor, change its ID to 2 and the baud rate to 57600.
- Since the motors will be mirrored, it is possible to have one motor spinning in the opposite direction. To fix this, change the motor's spinning direction by ticking the box for Bit 0 - Reverse mode under the Drive mode tab.
- On the Raspberry Pi, configure the latency_timer to 1 instead of 16 by running the following commands or following the instructions form the [official documentation](https://emanual.robotis.com/docs/en/parts/interface/u2d2/#linux).
```
cat /sys/bus/usb-serial/devices/ttyUSB0/latency_timer
echo 1 > /sys/bus/usb-serial/devices/ttyUSB0/latency_timer
cat /sys/bus/usb-serial/devices/ttyUSB0/latency_timer
```
- After configuring the motors, connect them to the U2D2 module and connect the U2D2 module to the Raspberry Pi and test the motors. If the motors aren't operating as expected use the python scripts from the `extra/test_motors` folder to identify the issue.

## Configuration for D435I Depth camera

- Since we are using a custom power supply for the Raspberry Pi, by default the USB ports are limited to 0.6A. To increase the current limit to 1.6A run the following command:
```
sudo nano /boot/firmware/config.txt
```
- And add the following line at the end of the file:
```
usb_max_current_enable=1
```
- After adding the line, save the file by pressing `Ctrl + X`, then `Y` and then `Enter` and reboot the Raspberry Pi by running the following command:
```
sudo reboot
```

## Extra - ROS2 Jazzy Installation with Docker

- If you don't have a machine with Ubuntu 24.04, you can use Docker to create a container with ROS2 Jazzy.
- After installing docker you can follow this [guide](https://docs.ros.org/en/jazzy/How-To-Guides/Installing-on-Raspberry-Pi.html)

<!-- - to get both lidar and depth camera working. firstly launch robot launch (withouth the depth camera plugged in) then plug in depth camera and launch d435i node with: -->

<!-- - To publish the depth image from the D435I camera run the following command:
```
ros2 run realsense2_camera realsense2_camera_node
```

- In RVIZ2 you can visualize the depth image by adding a new image topic and selecting the `/camera/camera/depth/image_rect_raw` topic.

- useful links: https://github.com/IntelRealSense/realsense-ros and https://dev.intelrealsense.com/docs/ros2-pointcloud-examples -->

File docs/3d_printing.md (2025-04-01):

# Printing and assembling instructions for OpenBot Waffle

- To preview the 3D model of the robot, you can use the following link: [OpenBot Waffle 3D Preview](https://cad.onshape.com/documents/e4455d89093a44267b1c8add/w/d262dbe7157cadda162aa249/e/e17b02729e8f8845fbf66276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)

# 3D Priting

The files needed for 3D printing the OpenBot Waffle robot are available in the `3d_files` folder. 

## Files `base0` and `base1` can be printed only with printers with build plate of at least 256 x 256 mm. 

For 3D printing we've used a BambuLab X1C printer. If you are using a BambuLab printer (A1, P1S or X1C) you can open `openbot_waffle_bambu.3mf` with Bamabu Studio and start printing. For the tires you have to use TPU filament and for the rest of the parts PLA filament. 

If you are using a different printer, in the `all_files` subfolder you can find all the parts in 3mf format. Print the tires with TPU filament and the rest of the parts with PLA filament. The only pieces that need supports are rims and the XL430 holders. 

If you are printing each parts individually use the next table to know the quantity of each part needed:

| Part Name | Quantity |
| --- | --- |
| `base0` | 1 |
| `base1` | 1 |
| `caster_wheel` | 2 |
| `rim` | 2 |
| `tire` | 2 |
| `xl430_holder` | 2 |
| `spacer_35mm` | 6 |
| `depth_holder_A` | 1 |
| `depth_holder_B` | 1 |
| `holder_u2d2` | 1 |
| `lidar_holder` | 1 |
| `imu_holder` | 1 |
| `pi_case_A` | 1 |
| `pi_case_B` | 1 |

# Assembly - Start after printing all the parts

 ## Step 1 - Attach components to their holders

 - Fix the Dynamixel XL430 motors in the XL430 holders with the screws provided with the motors.
 - Glue the tires to the rims.
 - Fix the wheels to the motors with the screws provided with the motors (4 screws is enough).
 - Attach the IMU unit to the IMU holder (before fixing the imu to the holder, connect 4 arduino cables to the IMU, red to Vin, black to GND and other two to SCL and SDA pins).
 - Attach depth holder A and B with a screw and nut then fix the depth camera to the holder.
 - Attach the Lidar to the lidar holder.

## Step 2 - Fix the components on the bottom base plate

 - Both for base0 and base1, to fix the parts in the exact position, refer to the [3D model of the robot](https://cad.onshape.com/documents/e4455d89093a44267b1c8add/w/d262dbe7157cadda162aa249/e/e17b02729e8f8845fbf66276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)
 - Using 3mm screws and nuts fix the motors, imu (before fixing it attach 4 cables to its VCC, SCL, SDA and GND pins), battery holder and u2d2 module to the base0 part.
 - Connect the motors to the U2D2 module, in the next image you can see how the Dynamixel motors are wired to the U2D2 module. Leave a USB cable connected to the U2D2 module that later will be connected to the Raspberry Pi.
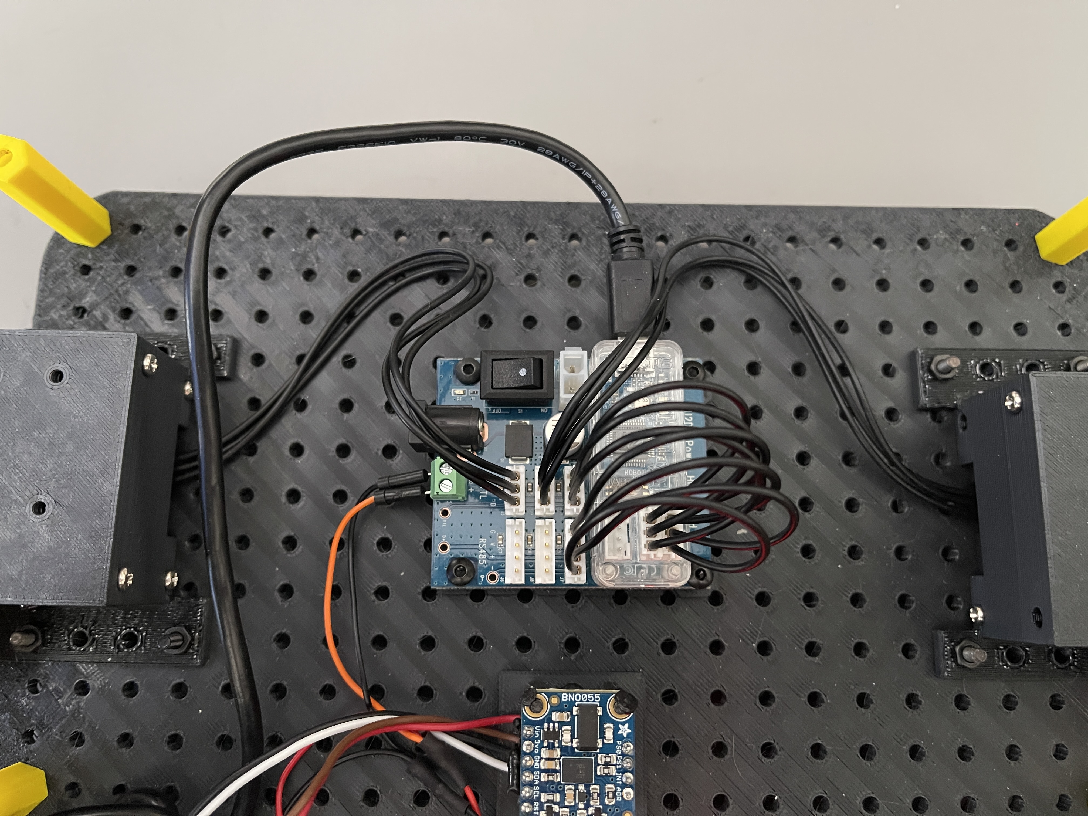
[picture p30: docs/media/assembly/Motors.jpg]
    
 - Glue the 5V 5A step down module to the base0 part.
 - Use zip ties to fix the cables to the plate.
 - Connect the battery holder to the 5V 5A step down module and to the U2D2 module. Leave an USB to Type C cablle connected to the 5V 5A step down module that later will power the Raspberry Pi. 
 - Make sure that the U2D2 module is powered directly from the battery since it needs 12 V to operate. If you power it from the 5V 5A step down module, it won't work.

 - Using 3mm screws and nuts fix the two caster wheels and six spacers to the base0 part.
 - After fixing all the components on the bottom plate, it should look like this:
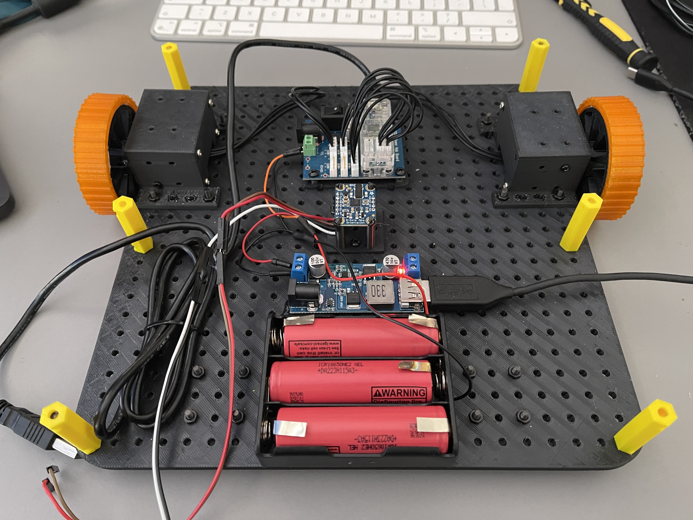
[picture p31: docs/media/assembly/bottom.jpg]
    

## Step 3 - Assemble the top plate of the robot

 - Screw on the base1 part the depth camera and lidar.
 - Fix on the base1 the raspberry pi holder then fix the raspberry pi to the holder.
 - Use zip ties to fix the cables from the lidar and depth camera to the plate.
 - Connect the Lidar and Depth camera to the Raspberry Pi via USB.
 - In the next image you can see how the top plate of the robot should look like.
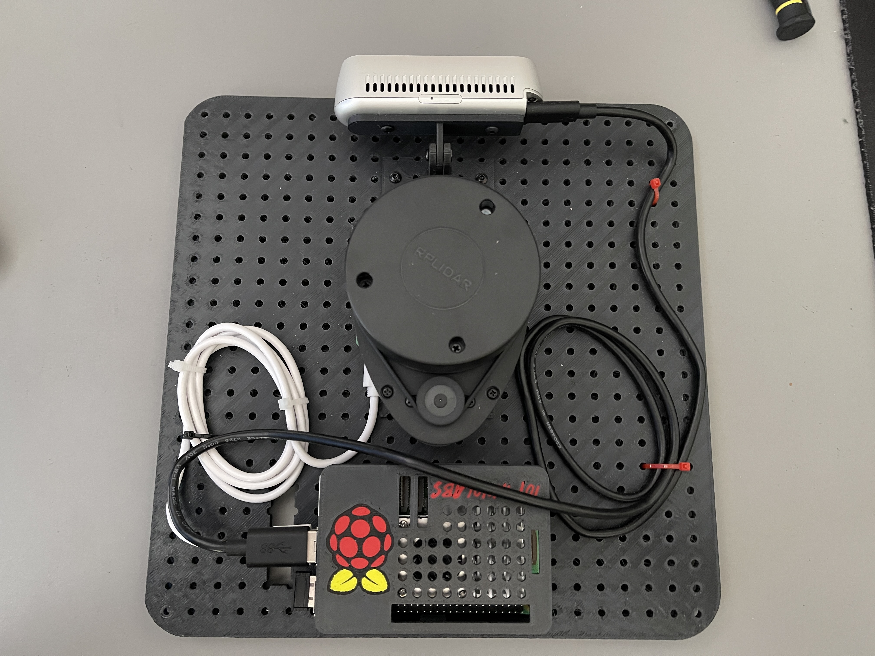
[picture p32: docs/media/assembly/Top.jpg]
      

 ## Step 4 - Assemble the robot by connecting the top and bottom plates via the spacers

 - Connect the base0 part to the base1 part with screws and nuts via the spacers. Pass the arduino cables (for the IMU) and the Type C cable through the hole of the base1 part (the hole under the lidar). Pass the cable from the U2D2 module through the hole of the base1 part (the hole next to the Raspberry Pi USB ports).
 - Connect the IMU to the Raspberry Pi following the next image. Use the hole from the upper base to pass the cables.
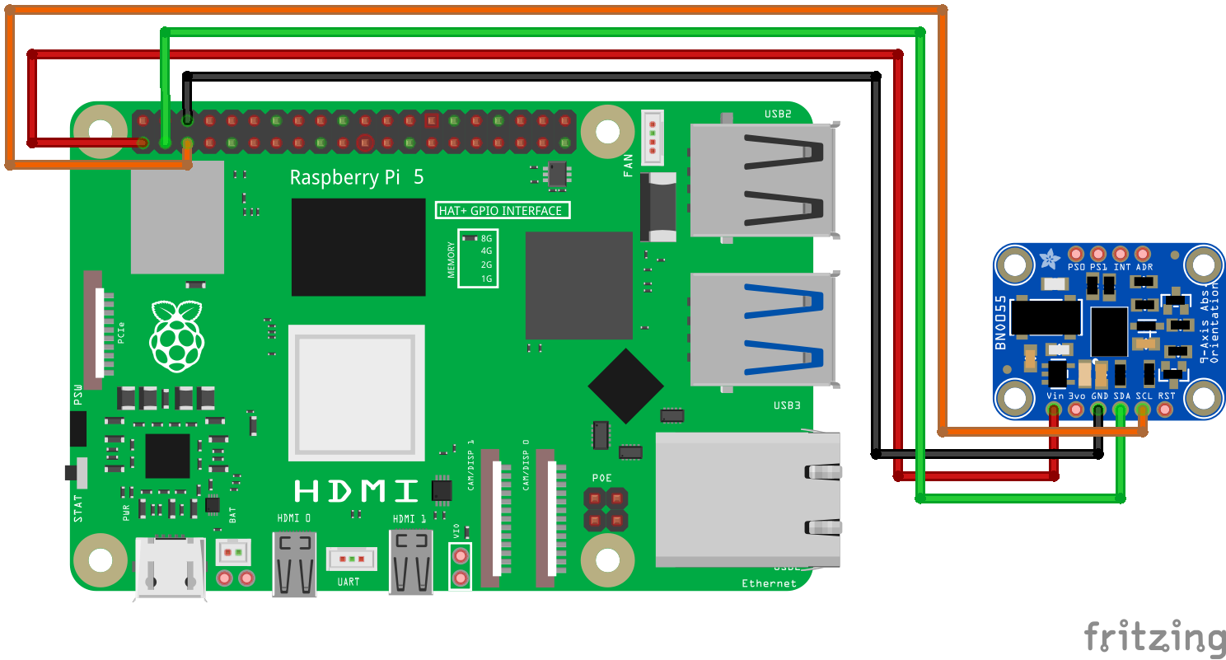
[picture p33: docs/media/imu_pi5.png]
 
 - Connect the U2D2 module to the Raspberry Pi via USB.

## Extra

 - When you are not using the robot, do not forget to remove the type C cable that powers it (even if you've turned off the raspberry pi). If you leave it connected, the battery will be drained in a few days (or even hours).

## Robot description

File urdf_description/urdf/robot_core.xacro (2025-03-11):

<?xml version="1.0"?>
<robot name="urdfbot" xmlns:xacro="http://ros.org/wiki/xacro">

  <xacro:property name="scl" value="0.001"/>
  <xacro:property name="PI" value="3.14159265335897931" />

    <link name="base_link">
    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
    <inertial>
      <mass value="10"/>
      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
    </inertial>
  </link>

  <link name="motor_left">
    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
    <inertial>
      <mass value="0.05"/>
      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
    </inertial>
  </link>

  <joint name="base_link_to_motor_left" type="fixed">
    <origin xyz="0.06 0.1 0.005" rpy="0 0 ${PI/2}"/>
    <parent link="base_link"/>
    <child link="motor_left"/>
  </joint>

  <link name="motor_right">
    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
    <inertial>
      <mass value="0.05"/>
      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
    </inertial>
  </link>

  <joint name="base_link_to_motor_right" type="fixed">
    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
    <origin xyz="0.06 -0.1 0.005" rpy="0 0 ${PI/2}"/>
    <parent link="base_link"/>
    <child link="motor_right"/>
  </joint>

  <link name="left_wheel">
    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
    <inertial>
      <mass value="0.05"/>
      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
    </inertial>
  </link>

  <joint name="motor_left_to_left_rim" type="continuous">
    <origin xyz="0.021 0.01 0.01425" rpy="0 0 0"/>
    <axis xyz="1 0 0"/>
    <parent link="motor_left"/>
    <child link="left_wheel"/>
  </joint>

  <link name="right_wheel">
    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
    <inertial>
      <mass value="0.05"/>
      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
    </inertial>
  </link>

  <joint name="motor_right_to_right_rim" type="continuous">
    <origin xyz="-0.021 0.01 0.01425" rpy="0 0 0"/>
    <axis xyz="1 0 0"/>
    <parent link="motor_right"/>
    <child link="right_wheel"/>
  </joint>

  <link name="caster_wheel_left">
    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
    <inertial>
      <mass value="0.01"/>
      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
    </inertial>
  </link>

  <joint name="base_link_to_caster_wheel_left" type="fixed">
    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
    <origin xyz="-0.09 0.06 0" rpy="0 0 0"/>
    <parent link="base_link"/>
    <child link="caster_wheel_left"/>
  </joint>

  <link name="caster_wheel_right">
    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
    <inertial>
      <mass value="0.01"/>
      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
    </inertial>
  </link>

  <joint name="base_link_to_caster_wheel_right" type="fixed">
    <origin xyz="-0.09 -0.06 0" rpy="0 0 0"/>
    <parent link="base_link"/>
    <child link="caster_wheel_right"/>
  </joint>

  <link name="u2d2_link">
    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
  </link>

  <joint name="base_link_to_u2d2_link" type="fixed">
    <origin xyz="0.05 0 0.005" rpy="0 0 0"/>
    <parent link="base_link"/>
    <child link="u2d2_link"/>
  </joint>

  <link name="battery_link">
    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
    <inertial>
      <mass value="0.15"/>
      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
    </inertial>
  </link>

  <joint name="base_link_to_battery_link" type="fixed">
    <origin xyz="-0.08 0 0.005" rpy="0 0 0"/>
    <parent link="base_link"/>
    <child link="battery_link"/>
  </joint>

  <link name="spacer_front_right_lvl_0">
    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
  </link>

  <joint name="base_link_to_spacer_front_right_lvl_0" type="fixed">
    <origin xyz="0.11 -0.11 0.005" rpy="0 0 0"/>
    <parent link="base_link"/>
    <child link="spacer_front_right_lvl_0"/>
  </joint>

  <link name="spacer_middle_right_lvl_0">
    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
  </link>

  <joint name="base_link_to_spacer_middle_right_lvl_0" type="fixed">
    <origin xyz="0 -0.11 0.005" rpy="0 0 0"/>
    <parent link="base_link"/>
    <child link="spacer_middle_right_lvl_0"/>
  </joint>

  <link name="spacer_back_right_lvl_0">
    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
  </link>

  <joint name="base_link_to_spacer_back_right_lvl_0" type="fixed">
    <origin xyz="-0.11 -0.11 0.005" rpy="0 0 0"/>
    <parent link="base_link"/>
    <child link="spacer_back_right_lvl_0"/>
  </joint>

  <link name="spacer_front_left_lvl_0">
    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
  </link>

  <joint name="base_link_to_spacer_front_left_lvl_0" type="fixed">
    <origin xyz="0.11 0.11 0.005" rpy="0 0 0"/>
    <parent link="base_link"/>
    <child link="spacer_front_left_lvl_0"/>
  </joint>

  <link name="spacer_middle_left_lvl_0">
    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
  </link>

  <joint name="base_link_to_spacer_middle_left_lvl_0" type="fixed">
    <origin xyz="0.0 0.11 0.005" rpy="0 0 0"/>
    <parent link="base_link"/>
    <child link="spacer_middle_left_lvl_0"/>
  </joint>

  <link name="spacer_back_left_lvl_0">
    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
  </link>

  <joint name="base_link_to_spacer_back_left_lvl_0" type="fixed">
    <origin xyz="-0.11 0.11 0.005" rpy="0 0 0"/>
    <parent link="base_link"/>
    <child link="spacer_back_left_lvl_0"/>
  </joint>
    
  <link name="lvl_1">
    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
  </link>

  <joint name="base_link_to_lvl_1" type="fixed">
    <origin xyz="0 0 0.04" rpy="0 0 0"/>
    <parent link="base_link"/>
    <child link="lvl_1"/>
  </joint>

  <link name="depth_holder_B">
    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
  </link>

  <joint name="lvl_1_to_depth_holder_B" type="fixed">
    <origin xyz="0.08 0 0.005" rpy="0 0 0"/>
    <parent link="lvl_1"/>
    <child link="depth_holder_B"/>
  </joint>

  <link name="dept_holder_A">
    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
  </link>

  <joint name="depth_holder_B_to_dept_holder_A" type="fixed">
    <origin xyz="0 0 0.027" rpy="0 0 0"/>
    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
    <parent link="depth_holder_B"/>
    <child link="dept_holder_A"/>
  </joint>


  <link name="pi5">
    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
  </link>

  <joint name="lvl_1_to_pi5" type="fixed">
    <origin xyz="-0.08 0.00 0.01" rpy="0 0 0"/>
    <parent link="lvl_1"/>
    <child link="pi5"/>
  </joint>

  <link name="lidar_holder">
    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
  </link>

  <joint name="lvl_1_to_lidar_holder" type="fixed">
    <origin xyz="0 0 0.005" rpy="0 0 0"/>
    <parent link="lvl_1"/>
    <child link="lidar_holder"/>
  </joint>

</robot>

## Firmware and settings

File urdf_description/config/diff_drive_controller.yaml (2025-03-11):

controller_manager:
  ros__parameters:
    update_rate: 10

    joint_state_broadcaster:
      type: joint_state_broadcaster/JointStateBroadcaster

    diff_drive_controller:
      type: "diff_drive_controller/DiffDriveController"
    
diff_drive_controller:
  ros__parameters:
    
    left_wheel_names: ["motor_left_to_left_rim"]
    right_wheel_names: ["motor_right_to_right_rim"]
    wheel_separation: 0.265
    wheel_radius: 0.0325
    cmd_vel_timeout: 0.5
    velocity_command_interface: "velocity"
    state_interface: "velocity"

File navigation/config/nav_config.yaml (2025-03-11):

amcl:
  ros__parameters:
    use_sim_time: False
    alpha1: 0.2
    alpha2: 0.2
    alpha3: 0.2
    alpha4: 0.2
    alpha5: 0.2
    base_frame_id: "base_link"
    beam_skip_distance: 0.5
    beam_skip_error_threshold: 0.9
    beam_skip_threshold: 0.3
    do_beamskip: false
    global_frame_id: "map"
    lambda_short: 0.1
    laser_likelihood_max_dist: 2.0
    laser_max_range: 100.0
    laser_min_range: -1.0
    laser_model_type: "likelihood_field"
    max_beams: 60
    max_particles: 2000
    min_particles: 500
    odom_frame_id: "odom"
    pf_err: 0.05
    pf_z: 0.99
    recovery_alpha_fast: 0.0
    recovery_alpha_slow: 0.0
    resample_interval: 1
    robot_model_type: "nav2_amcl::DifferentialMotionModel"
    save_pose_rate: 0.5
    sigma_hit: 0.2
    tf_broadcast: true
    transform_tolerance: 1.0
    update_min_a: 0.2
    update_min_d: 0.25
    z_hit: 0.5
    z_max: 0.05
    z_rand: 0.5
    z_short: 0.05
    scan_topic: scan

amcl_map_client:
  ros__parameters:
    use_sim_time: False

amcl_rclcpp_node:
  ros__parameters:
    use_sim_time: False

bt_navigator:
  ros__parameters:
    use_sim_time: False
    global_frame: map
    robot_base_frame: base_link
    odom_topic: /odom
    default_bt_xml_filename: "navigate_w_replanning_and_recovery.xml"
    bt_loop_duration: 10
    default_server_timeout: 20
    enable_groot_monitoring: True
    groot_zmq_publisher_port: 1666
    groot_zmq_server_port: 1667
    # plugin_lib_names:
    # - nav2_compute_path_to_pose_action_bt_node
    # - nav2_compute_path_through_poses_action_bt_node
    # - nav2_follow_path_action_bt_node
    # - nav2_back_up_action_bt_node
    # - nav2_spin_action_bt_node
    # - nav2_wait_action_bt_node
    # - nav2_clear_costmap_service_bt_node
    # - nav2_is_stuck_condition_bt_node
    # - nav2_goal_reached_condition_bt_node
    # - nav2_goal_updated_condition_bt_node
    # - nav2_initial_pose_received_condition_bt_node
    # - nav2_reinitialize_global_localization_service_bt_node
    # - nav2_rate_controller_bt_node
    # - nav2_distance_controller_bt_node
    # - nav2_speed_controller_bt_node
    # - nav2_truncate_path_action_bt_node
    # - nav2_goal_updater_node_bt_node
    # - nav2_recovery_node_bt_node
    # - nav2_pipeline_sequence_bt_node
    # - nav2_round_robin_node_bt_node
    # - nav2_transform_available_condition_bt_node
    # - nav2_time_expired_condition_bt_node
    # - nav2_distance_traveled_condition_bt_node
    # - nav2_single_trigger_bt_node
    # - nav2_is_battery_low_condition_bt_node
    # - nav2_navigate_through_poses_action_bt_node
    # - nav2_navigate_to_pose_action_bt_node
    # - nav2_remove_passed_goals_action_bt_node
    # - nav2_planner_selector_bt_node
    # - nav2_controller_selector_bt_node
    # - nav2_goal_checker_selector_bt_node

bt_navigator_rclcpp_node:
  ros__parameters:
    use_sim_time: False

controller_server:
  ros__parameters:
    use_sim_time: False
    controller_frequency: 10.0
    min_x_velocity_threshold: 0.001
    min_y_velocity_threshold: 0.5
    min_theta_velocity_threshold: 0.001
    failure_tolerance: 0.3
    progress_checker_plugin: "progress_checker"
    goal_checker_plugins: ["general_goal_checker"] 
    controller_plugins: ["FollowPath"]

    # Progress checker parameters
    progress_checker:
      plugin: "nav2_controller::SimpleProgressChecker"
      required_movement_radius: 0.5
      movement_time_allowance: 10.0
    
    general_goal_checker:
      stateful: True
      plugin: "nav2_controller::SimpleGoalChecker"
      xy_goal_tolerance: 0.25
      yaw_goal_tolerance: 0.25

    # DWB parameters
    FollowPath:
      plugin: "dwb_core::DWBLocalPlanner"
      debug_trajectory_details: True
      min_vel_x: 0.0
      min_vel_y: 0.0
      max_vel_x: 0.22
      max_vel_y: 0.0
      max_vel_theta: 1.0
      min_speed_xy: 0.0
      max_speed_xy: 0.22
      min_speed_theta: 0.0
      # Add high threshold velocity for turtlebot 3 issue.
      # https://github.com/ROBOTIS-GIT/turtlebot3_simulations/issues/75
      acc_lim_x: 2.5
      acc_lim_y: 0.0
      acc_lim_theta: 3.2
      decel_lim_x: -2.5
      decel_lim_y: 0.0
      decel_lim_theta: -3.2
      vx_samples: 20
      vy_samples: 0
      vtheta_samples: 40
      sim_time: 2.0
      linear_granularity: 0.05
      angular_granularity: 0.025
      transform_tolerance: 0.2
      xy_goal_tolerance: 0.05
      trans_stopped_velocity: 0.25
      short_circuit_trajectory_evaluation: True
      stateful: True
      critics: ["RotateToGoal", "Oscillation", "BaseObstacle", "GoalAlign", "PathAlign", "PathDist", "GoalDist"]
      BaseObstacle.scale: 0.02
      PathAlign.scale: 32.0
      PathAlign.forward_point_distance: 0.1
      GoalAlign.scale: 24.0
      GoalAlign.forward_point_distance: 0.1
      PathDist.scale: 32.0
      GoalDist.scale: 24.0
      RotateToGoal.scale: 32.0
      RotateToGoal.slowing_factor: 5.0
      RotateToGoal.lookahead_time: -1.0

controller_server_rclcpp_node:
  ros__parameters:
    use_sim_time: False
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

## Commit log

2025-03-14 update docs (assembly, soft and teleop) and add joystick teleop
2025-03-18 update parameters for SLAM
    [controller.yaml]
2025-03-24 add depth camera and update docs
2025-04-01 update camera config for publishing rgbd images and update docs
